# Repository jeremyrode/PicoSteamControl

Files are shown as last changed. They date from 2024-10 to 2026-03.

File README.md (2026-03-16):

# PicoSteamControl
This project implements a new Raspberry Pi Pico based control for a [Leisure Steam One Touch LS series steam generator](https://leisure-steam.com/product-category/steam-generators/1-touch-steam-unit/).

The factory control PCB was misbehaving, and I have wanted to implement an automatic self-flush to clean the tank, so I thought it would be a good challenge to replace it with a Raspberry Pi Pico.

This is my first MicroPython project.  I was originally implementing this system in C, but when I started down the path to connect a Pico W to WiFi, I decided to try out MicroPython and I was blown away by the power and rapid development/test cycles.

I mostly think this project might be interesting to people because of a few new ideas that I have not seen documented well in the wild:

# New ideas:

This project served as a testbed for 3 new ideas that I wanted to try:
- Status Logging and Timestamping though WiFi
- Capacitive Touch Sensing via a PIO State Machine
- New Ideal Diode Peak Detector CT Interface

## Status Logging and Timestamping though WiFi

A major reason I was implementing much of my IoT work with boards that run full Linux (usually a Raspberry Pi Zero W) is logging and timestamping functionality.  Many of these IoT systems are very difficult to debug without a persistent log that is timestamped.  Both storing and retrieving persistent logs (to some sort of nonvolatile memory) and getting real time (UTC) on a microcontroller are difficult.

Here, this is solved by sending my log messages out to Raspberry Pi with NTP running via the network and urequests libraries:

```python
def logWifi(logmessage):
    print('Log: ' + logmessage)
    res = requests.post(secrets.url, data = logmessage)
```

Remarkably simple and effective, this server could easily serve many Pico W boards. See main.py for the full code with WiFi reconnection, and error handling.  [The secrets.url uses a config file to not check in WiFi passwords or local IPs to a public Git.]( https://www.coderdojotc.org/micropython/wireless/02-connecting-to-wifi/ "MicroPython WiFi Info")

The logWifi() function in main.py takes the log request and sends it to a http server (SteamLogger.js) running in Node.js that timestamps it and writes it to a file.

```node
const server = http.createServer((req, res) => {
  if (req.method === 'POST') {
    let data = '';
    req.on('data', chunk => {
      data += chunk.toString();
    });
    req.on('end', () => {
      let curDate = new Date();
      let dateStr = curDate.toString();
      message = dateStr.slice(0,dateStr.length-33) + ' ' + data; //Prepend Time to message
      console.log(message);
      logfile.write(message + '\n')
      res.end('OK');
    });
  }
});
```
Note that this code was upgraded into batch mode via Gemini.

## Capacitive Touch Sensing via PIO State Machine

After discovering that the control button on the LS1 one touch is a capacitive membrane switch, I investigated specific ICs that detect capacitive touch sensing, but this is a perfect task for a PIO state machine. This PIO-based detection ended up very reliable and has very good dynamic range: Around 250K cycles for the untouched state, and with a strong push increasing this to 6-8M cycles.  A logging function serves to quantify the reliability. 

Here is a very unoptimized PIO state machine that charges a capacitive touch sensor via an output pin and a resistor, then cycle counts the time to discharge.
[I’ve broke this out into its own repository]( https://github.com/jeremyrode/RaspPiPicoTouchSensor "RaspPiPicoTouchSensor Repo"), and I might try to optimize it eventually.

```
pull(block)                 # Get charge delay val     
mov(x,osr)                  # Load charge delay val    
wrap_target()               # Only do the above once   
mov(y, invert(null))        # Set Y to Large (All Ones)
set(pins, 1)                # Start Charging           
label("innerloop")                                     
jmp(pin, "loopescape")      # If Pin is High, Escape   
jmp(y_dec, "innerloop")     # Loop and decrement Y     
label("loopescape")                                    
mov(isr,y)                  # Move Y to CPU SR         
set(pins, 0)                # Discharge                
push(noblock)               # Push Y                   
mov(y,x)                    # Load charge delay val    
label("chargeloop")                                    
jmp(y_dec, "chargeloop")     # If !Zero, X-- and loop  
wrap()                                                 
```

### How it Works

This code uses a PIO state machine to repeatedly charge and discharge the touch sensor detecting a change in capacitance via the time-to-charge.  The touch sensor is charged via an output pin connected through 1-megaohm resistor (R1 on schematic) giving a RC time delay that can be measured by an input pin connected directly to the touch sensor.

The PIO state machine starts by getting the discharge time via an initial value written to the PIO state machine, that is moved to scratch register X.  This is necessary, as the PIO SET instruction is limited to 31, which is nowhere near the necessary value* (1,250,000).  The state machine then sets Y to all ones, sets the charge pin to "1", and counts down (via the "innerloop") until the jump pin goes low via RC discharge.  The jump escapes the loop (via jumping to "loopescape").  The Y value is outputted by moving Y to the input shift register (ISR) and pushing to the FIFO.  The push is nonblocking, to keep the detections going, but the FIFO will go stale if it's not read periodically.  To prepare for the next detection the charge pin is set to discharge "0", and then the discharge delay is performed, but preserving the charge delay value stored in scratch register X, to Y, then looping via “chargeloop”.  At this point, we return to wrap_target(), which repeats everything (except loading the charge delay to scratch register X).

The user space code calibrates the baseline charge time with an IIR filter, and if a difference (here 4_000_000 cycles or 32 ms) in the charge time is detected a touch event is registered.  The touch detection is debounced via a time delay gate, as a single human-timescale touch event can trigger multiple PIO detections.

*Yes, I’m aware that large values in scratch registers can be set via the bit-reverse function of the MOV instruction, but these are a bit too large, as the smallest value is a SET of 16 (0b10000), bit reversed is 2^27, which is a delay of 1 second (2^27 / 125 MHz).

```python
baseline = 350_000 # Inital state for baseline IIR Value for touch detection (350_000, connected, 4_000 bare PCB)
touch_threshold = 4_000_000 #Threshold above baseline for a touch (4_000_000, connected, 4_000 bare PCB)
time_between_touches_ms = 1000 #Debounce time for a touch
DATA_IIR_CONST = 1000  # Filtering constant for the IIR filter
sm.put(1_250_000, 0)  #This sets Charging Delay and detection rate in SM clock cycles (10 ms)
while True:
    curval = 4_294_967_295 - sm.get() #State Machine counts down from 2^32
    if time.ticks_diff(time.ticks_ms(), last_touch) > time_between_touches_ms: #Not a multi-touch event
        if curval > baseline + touch_threshold: #We have a touch event
            last_touch = time.ticks_ms()
            print('Touch')
        else: #Only start taking button stats after the touch event has passed
            baseline = curval / DATA_IIR_CONST + baseline * (DATA_IIR_CONST - 1) / DATA_IIR_CONST #Take Baseline Stats
```

Here the python sets the discharge delay via sm.put().  An infinite loop pulls the discharge value and changes it into delay counts by subtracting from 2^32.  Here the detection is debounced via a timestamp and compared to a threshold value above a baseline non-touched value.  This code adapts the baseline capacitance via an infinite first-order impulse response (IIR) filter that adapts to any slow varying baseline capacitance.

## New Ideal Diode Peak Detector CT Interface

Interfacing to Current Transformers (CTs) is a real pain; either one needs to bias the signal in the middle of the ADC range, and sample fast enough to capture the 60 Hz sine wave, extracting the RMS, or a diode envelope detector can be used.  The simple diode envelope detector simplifies the ADC reading, as the output signal is DC, but the diode turn-on voltage makes the transfer function non-linear when the signal from the CT is below the diode turn-on voltage, making the current measurement inaccurate at low current.

Here, I’ve tried to make an ideal diode based peak detector (with gain) out of a non-inverting op amp driving though a diode.  Ideally this should both make the ADC readout much simpler and more accurate, as the output is DC, and the time constant can be set via a capacitor, and make the CT more accurate as the burden resistor can be sized optimally for the CT, with the op-amp gain used to optimally fill the ADC range from the typically lower voltage from a CT in the linear regime.

# Schematic:

The factory control board was replaced with a quad relay board from amazon, wired directly to a RJ45 (J2) breakout board from Spark Fun (Pins 8-3). This relay board replaces the factory control board, and is wired into the 220V fill solenoid, drain valve, and the 50A heater contactor.  The relay board is an active low (open collector) on pins 4-7, VCC on pin 4 and ground on pin 1.  I wired a 1600:1 50A Current Transformer (CT) to pins 1 and 2.

The factory touchpad with LED is wired to J1.  From measuring with a meter, the power LED is on Pins 1 and 2 of the RJ12 connector (J1).  The capacitive touch sensor is on pin 4.  I think the ground shield of the cap sensor is on pin 3.

Note that this is the schematic that I built on a proto board with parts on hand.  A PCB with a proper ground is in the PCB directory.

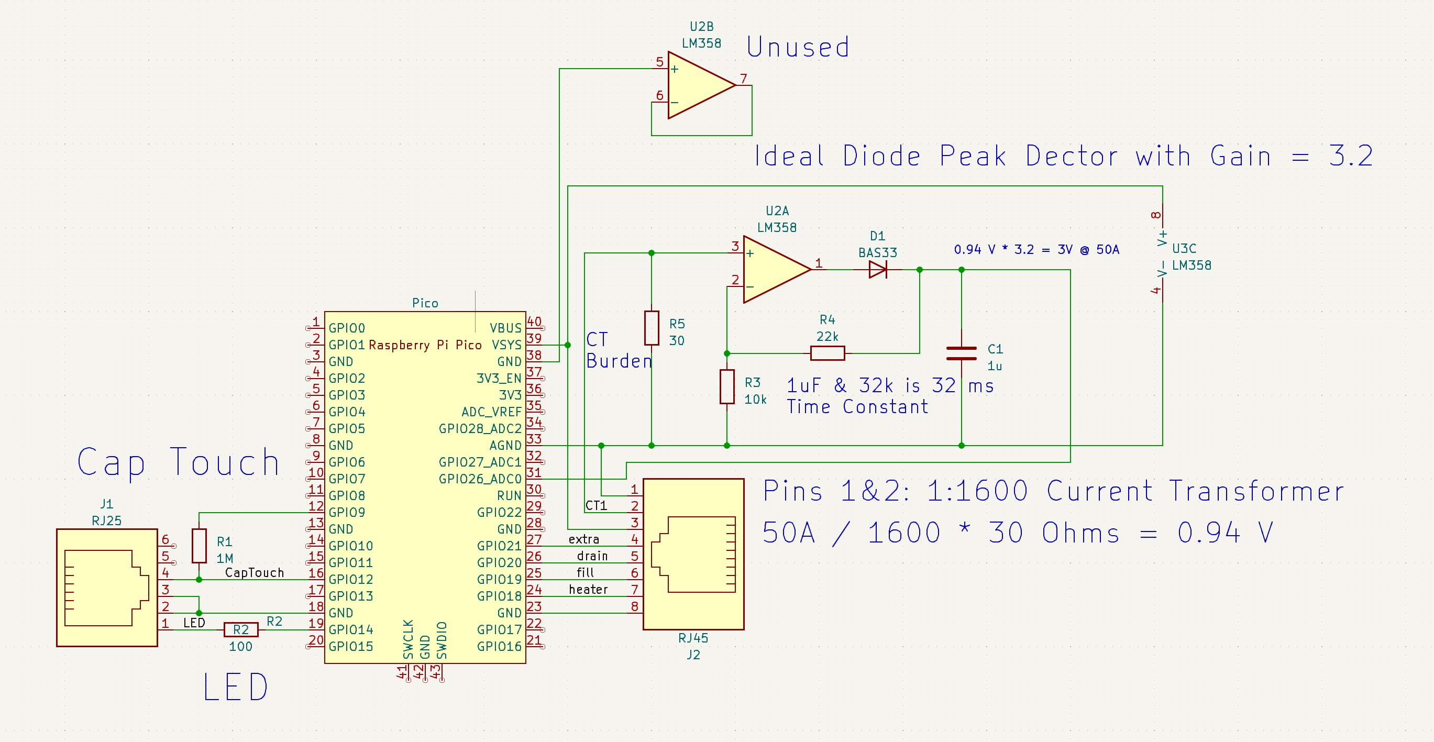
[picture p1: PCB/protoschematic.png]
Schematic


The CT burden resistor (R5) is set at 30 Ohms, calculated for good CT linearity.  The output voltage from the burdgen resistor goes to an op-amp (U2A). Here U2A with feedback around a diode (D1) forms an ideal diode, with feedback though a voltage divider formed by R4/R3, here with a voltage gain of 3.2X.  A 1uF capacitor (C1) stores the peak voltage from the diode (envelope detector), with a discharge time constant of ~32ms (1uF & 32k Ohms).  This voltage is converted by ADC0 of the Pico.

Testing and simulations show this time constant isn't nearly enough by a couple of orders of magnitude, the proper calculation should be how much voltage sag the sampling capacitor has over the 1/60 Hz cycle and this calculation results in the resistor sum greater than a megaohm for 1 LSB of a 12-bit ADC.  Achieving the time constant with larger values can cause opamp instability and overshoot when the current changes.

The unused is set to an non-inverting amp of gain 1 to ground, [as per recommendation.]( https://www.ti.com/lit/ab/sboa204a/sboa204a.pdf)  Note that the op amp used here needs to be rated for a common-mode voltage at the bottom rail (here ground), but not the top rail, as there is headroom between the 3.3V maximum output and the 5V supply.  The [LM358 is rated for VCM down to V- but only to V+ - 2V.](https://www.ti.com/product/LM358#tech-docs)

# Future Ideas
- Higher touch threshold for on than off
- Low/High via separate contactors for each heating element
- Optimize the PIO touch detection
- Single Pin touch detection

## Single Pin Optimized PIO touch detection

Single pin sans resistor touch detection is very possible.  The Pico has pin pull down functionality (it’s on by default), and the IO directionally can be set dynamically via PINDIRS.  The state machine could be made tighter by both slowing down the clock rate such that the delay can be implemented by the SET instruction, and the SIDESET functionality can save a few instructions.

# Errata Discovered for time.ticks_diff()

time.ticks_diff() doesn't seem to like intervals over a few days, the code was hanging.  I have changed the code to use a boolean to keep toggle the state, rather than rely on elapsed time, which seems to not work after a few days.

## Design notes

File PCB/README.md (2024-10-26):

# PicoSteamControl Schematic

No PCB yet, just the schematic I build on a protoboard

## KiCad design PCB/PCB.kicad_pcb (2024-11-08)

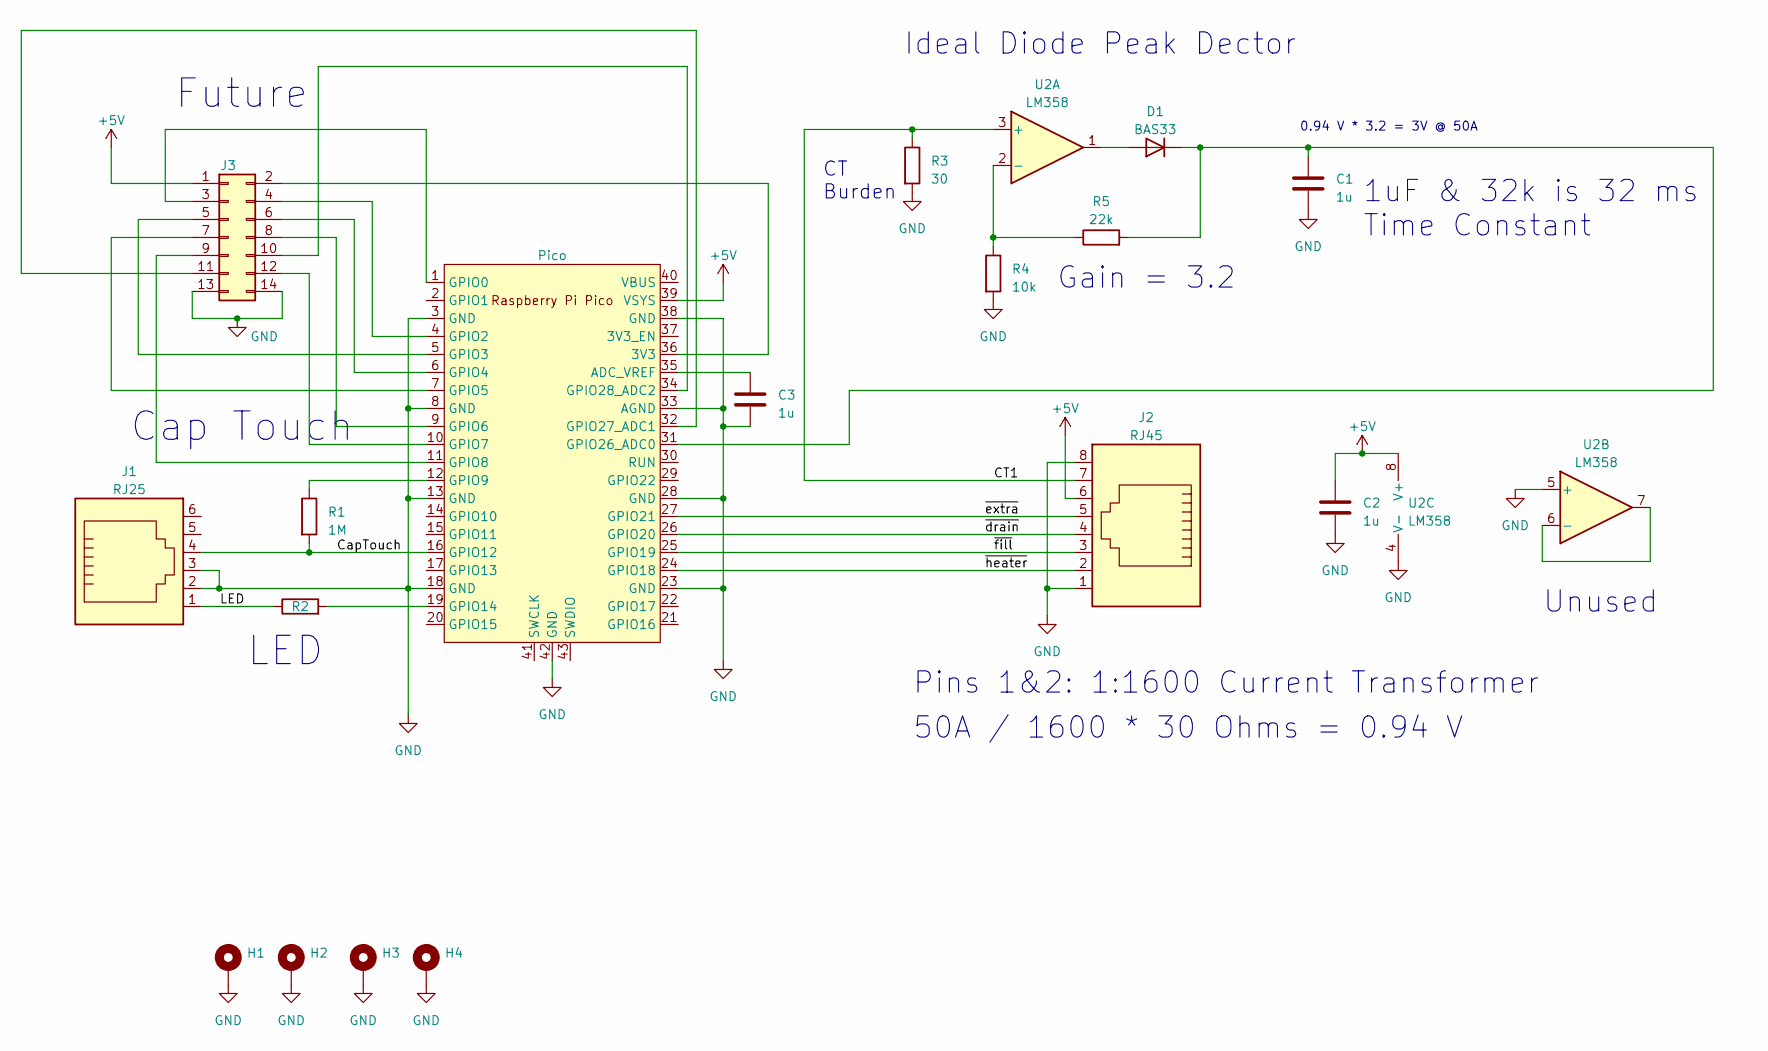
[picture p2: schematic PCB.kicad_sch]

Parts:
C1, C2, C3: 1u; C_0805_2012Metric_Pad1.18x1.45mm_HandSolder
D1: BAS33; D_DO-35_SOD27_P7.62mm_Horizontal
H1, H2, H3, H4: MountingHole_Pad; MountingHole_2.7mm_M2.5_Pad
J1: RJ25; RJ25_Wayconn_MJEA-660X1_Horizontal
J2: RJ45; RJ45_Amphenol_54602-x08_Horizontal
J3: Conn_2Rows-07Pins; PinHeader_2x07_P2.54mm_Vertical
R1: 1M; R_0805_2012Metric_Pad1.20x1.40mm_HandSolder
R2: 100; R_0805_2012Metric_Pad1.20x1.40mm_HandSolder
R3: 30; R_0805_2012Metric_Pad1.20x1.40mm_HandSolder
R4: 10k; R_0805_2012Metric_Pad1.20x1.40mm_HandSolder
R5: 22k; R_0805_2012Metric_Pad1.20x1.40mm_HandSolder
U1: Pico; RPi_Pico_SMD
U2: LM358; DIP-8_W10.16mm

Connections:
+5V: C2.1, J2.6, J3.1, U1.39 (VSYS), U2.8 (V+)
/CT1: J2.7, R3.1, U2.3 (+)
/CapTouch: J1.4, R1.2, U1.16 (GPIO12)
/LED: J1.1, R2.1
/~drain: J2.4, U1.26 (GPIO20)
/~extra: J2.5, U1.27 (GPIO21)
/~fill: J2.3, U1.25 (GPIO19)
/~heater: J2.2, U1.24 (GPIO18)
GND: C1.2, C2.2, C3.2, H1.1, H2.1, H3.1, H4.1, J1.2, J1.3, J2.1, J2.8, J3.13, J3.14, R3.2, R4.2, U1.3 (GND), U1.8 (GND), U1.13 (GND), U1.18 (GND), U1.23 (GND), U1.28 (GND), U1.33 (AGND), U1.38 (GND), U1.42 (GND), U2.4 (V-), U2.5 (+)
unnamed: D1.2 (A), U2.1
unnamed: C1.1, D1.1 (K), R5.2, U1.31 (GPIO26_ADC0)
unnamed: J3.2, U1.36 (3V3)
unnamed: J3.3, U1.1 (GPIO0)
unnamed: J3.4, U1.4 (GPIO2)
unnamed: J3.5, U1.5 (GPIO3)
unnamed: J3.6, U1.6 (GPIO4)
unnamed: J3.7, U1.7 (GPIO5)
unnamed: J3.8, U1.9 (GPIO6)
unnamed: J3.9, U1.11 (GPIO8)
unnamed: J3.10, U1.34 (GPIO28_ADC2)
unnamed: J3.11, U1.32 (GPIO27_ADC1)
unnamed: J3.12, U1.10 (GPIO7)
unnamed: C3.1, U1.35 (ADC_VREF)
unnamed: R1.1, U1.12 (GPIO9)
unnamed: R2.2, U1.19 (GPIO14)
unnamed: R4.1, R5.1, U2.2 (-)
unnamed: U2.6 (-), U2.7

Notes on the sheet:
Unused
1uF & 32k is 32 ms Time Constant
Ideal Diode Peak Dector
LED
Future
CT Burden
50A / 1600 * 30 Ohms = 0.94 V
Gain = 3.2
Cap Touch
0.94 V * 3.2 = 3V @ 50A
Pins 1&2: 1:1600 Current Transformer

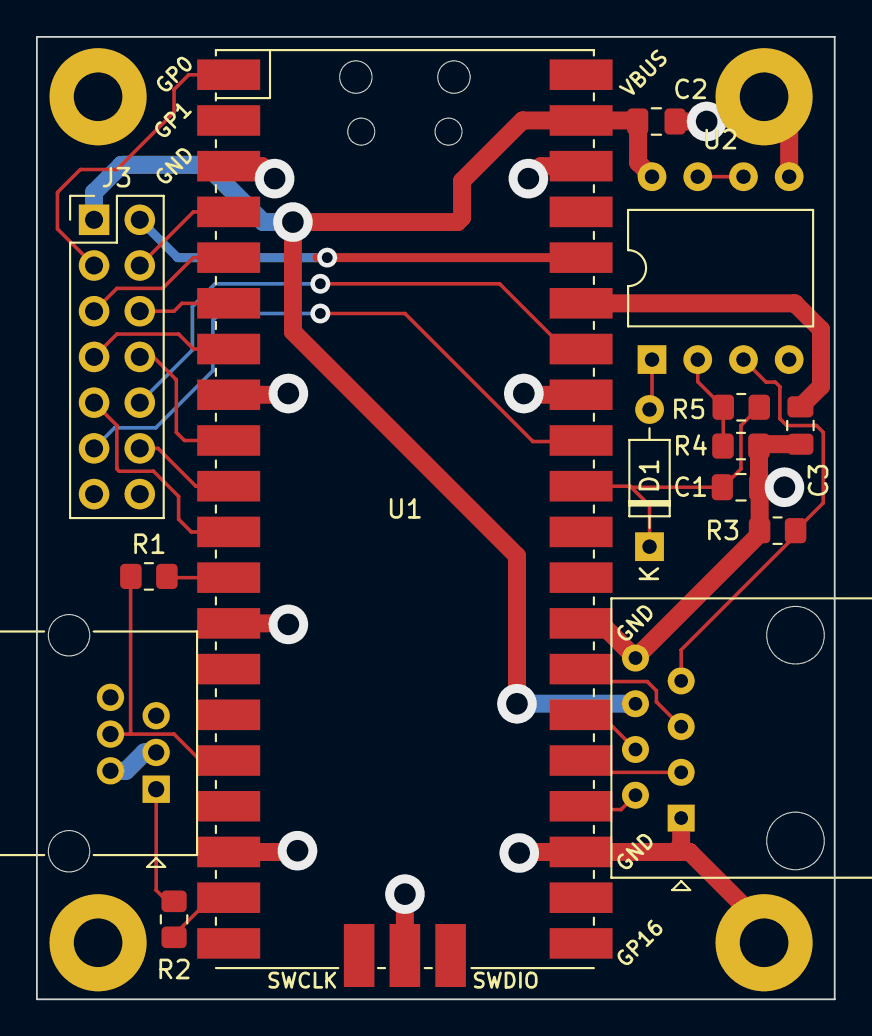
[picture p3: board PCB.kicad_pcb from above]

Board: 4 copper layers, 44.3 x 53.5 mm, 18 parts (0 on the bottom side), 27 nets.

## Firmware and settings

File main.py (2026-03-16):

import time
import machine
import rp2
import network
import secrets
import urequests as requests
print('boot')
## Pin Setup / LED
shower_led = machine.Pin(14, mode=machine.Pin.OUT, pull=None, value=0)
wled = machine.Pin("LED", machine.Pin.OUT) #Pico W LED
heater = machine.Pin(18, mode=machine.Pin.OPEN_DRAIN, pull=None, value=1)
fill = machine.Pin(19, mode=machine.Pin.OPEN_DRAIN, pull=None, value=1)
drain = machine.Pin(20, mode=machine.Pin.OPEN_DRAIN, pull=None, value=1)
extra =  machine.Pin(21, mode=machine.Pin.OPEN_DRAIN, pull=None, value=1)
# Turn off internal pull up on jmp pin
sense = machine.Pin(12, mode=machine.Pin.IN, pull=None)
adc = machine.ADC(machine.Pin(26))     # create ADC object on ADC pin
# Let us know were booting
wled.value(1)
shower_led.value(1)
# WLAN Setup
wlan = network.WLAN(network.STA_IF)
# Timers
statetimer = machine.Timer()
currentLogTimer = machine.Timer()
# Globals
state = 'off' # off / filling / heat / cool / flush / quickdrain
flush_count = 4 #Zero means flush done
log_queue = [] # Queue for log messages from timers
baseline = 350_000 # Inital state for baseline IIR Value for touch detection (350_000, connected, 4_000 bare PCB)
touch_threshold = 4_000_000 #Threshold above baseline for a touch (4_000_000, connected, 4_000 bare PCB)
time_between_touches_ms = 1000 #Debounce time for a touch
touch_armed = False
current_raw = 0 #Inital State for current IIR
DATA_IIR_CONST = 1000  # Filtering constant for the IIR filters
time_between_status_ms = 1000 * 60 * 60 * 12 # How often to log status
wifilog = True # If log to wifi
max_val = 0
# Helper to add to queue and print
def addLog(msg):
    print('Log:', msg)
    if len(log_queue) > 50:
        log_queue.pop(0) # Keep queue capped to protect RAM
    log_queue.append(msg)

# Logging Function
def flushWifiLogs(logmessage):
    if not wifilog:
        return True # Clear queue if logging is disabled

    if not wlan.isconnected():
        print(f"Reconnecting to WiFi Network Name: {secrets.ssid}")
        try:
            wlan.active(True)
            wlan.connect(secrets.ssid, secrets.password)
        except OSError as error:
            print(f'Connect error is {error}')
            return False
        except Exception as e:
            print(f"An unknown connect error occurred: {e}")
            return False
        print('Waiting for connection...')
        counter = 0
        while not wlan.isconnected():
            # wdt.feed()
            time.sleep(1)
            print(counter, '.', sep='', end='')
            counter += 1
            if counter > 20:
                print('Failed to Connect')
                return False
        print('\nIP Address: ', wlan.ifconfig()[0])
        
    try:
        print("Trying to Post")
        api_key = getattr(secrets, 'STEAM_LOGGER_SECRET_KEY', 'default_key')
        headers = {'x-api-key': api_key, 'Content-Type': 'text/plain'}
        res = requests.post(secrets.url, data=logmessage, headers=headers)
        print("Posted")
    except: #Need to catch this or we stop
        print("Log Failed, Post Error")
        return False
    else:
        success = False
        if res.text != 'OK':
            print('Unexpected Post Response:', res.text)
        else:
            success = True
        res.close()
        return success
    
# Helper functions to make code readable, and to add logging
def logCurrent(callingtimer):
    addLog(f"C: {round(current_raw)}")

def ledOn():
    wled.value(1) #Turn on board LED
    shower_led.value(1) #Turn on Shower LED

def ledOff():
    wled.value(0) #Turn off LED
    shower_led.value(0) #Turn off Shower LED

def heat_on():
    heater.value(0) #Turn on Heat, Active Low
    currentLogTimer.init(mode=machine.Timer.PERIODIC,period=30_000,callback=logCurrent) 

def heat_off():
    heater.value(1) #Turn off Heat, Active Low
    currentLogTimer.deinit() #No need to log anymore

def fill_open():
    fill.value(0) #Start Filling

def fill_closed():
    fill.value(1) #Stop Filling

def drain_open():
    drain.value(0) #Start Draining

def drain_closed():
    drain.value(1) #Stop Draining

def is_drain_closed():
    return drain.value()

# State Functions
def goFlush(callingtimer):
    global flush_count, state
    state = 'flush'
    fill_open() #Start Filling
    if not is_drain_closed(): #We are not draining
         drain_open() #Start Draining
         addLog(f"Flush Drain Cycle: {flush_count}")
    else:
        drain_closed() #Stop Draining
        flush_count -= 1 # Done with this flush round
        addLog(f"Flush Fill Cycle: {flush_count}")
    if flush_count > 0: #More flushes to go, recursive
        statetimer.init(mode=machine.Timer.ONE_SHOT,period=300_000,callback=goFlush) # Cycle the Flush 5 mins (300_000)
    else:
        addLog("Final Long Drain Cycle")
        drain_open() #Start Draining
        fill_closed()   # Stop Filling
        statetimer.init(mode=machine.Timer.ONE_SHOT,period=3_600_000,callback=goOff) # Final Drain Cycle 60 mins (3_600_000)
             
def goHeat(callingtimer):
    global state
    state = 'heat'
    ledOn() #Turn on LED
    fill_open() #Keep Filling
    heat_on() # Start Heat
    drain_closed() # Stop Drain
    statetimer.init(mode=machine.Timer.ONE_SHOT,period=900_000,callback=goCool) # Auto Off Timer 15 mins (900_000)
    addLog('Heat State')

def goCool(callingtimer):
    global flush_count, state
    state = 'cool'
    ledOff()
    fill_closed()   # Stop Filling
    heat_off() # Stop Heat
    drain_closed() # Stop Drain
    flush_count = 4 #Queue up some flushing
    statetimer.init(mode=machine.Timer.ONE_SHOT,period=3_600_000,callback=goFlush) # Cooling Timer 60 mins (3_600_000)
    addLog('Cool State')
    
def goFill(callingtimer):
    global state
    state = 'filling'
    ledOn() #Turn on LED
    fill_open() #Start Filling
    heat_off() # Stop Heat
    drain_closed() # Stop Drain
    statetimer.init(mode=machine.Timer.ONE_SHOT,period=20_000,callback=goHeat) # Fill Timer, 20s (20_000)
    addLog('Fill State')
   
def goOff(callingtimer):
    global state
    state = 'off'
    ledOff() #Turn off LED
    fill_closed()   # Stop Filling
    heat_off() # Stop Heat
    drain_closed() # Stop Drain
    statetimer.deinit()
    addLog('Off State')

def goQuickDrain(callingtimer):
    global state
    state = 'quickdrain'
    ledOff() #Turn off LED
    fill_closed()   # Stop Filling
    heat_off() # Stop Heat
    drain_open() #Start Draining
    statetimer.init(mode=machine.Timer.ONE_SHOT,period=600_000,callback=goOff) # Final Drain Cycle 10 mins (600_000)
    addLog('Quick Drain')
    
def printTouchStatus():
    global max_val, baseline, last_status
    addLog(f"Base: {round(baseline)} Max:  {round(max_val - baseline)}")
    max_val = 0
    last_status = time.ticks_ms()

# Touch Sensor PIO State Machine
@rp2.asm_pio(set_init=rp2.PIO.OUT_LOW, autopull=False, pull_thresh=32, autopush=False, push_thresh=32)
def detectTouch():                                         # type: ignore
    pull(block)                 # Get charge delay val     # type: ignore
    mov(x,osr)                  # Load charge delay val    # type: ignore
    wrap_target()               # Only do the above once   # type: ignore
    mov(y, invert(null))        # Set Y to Large (All Ones)# type: ignore
    set(pins, 1)                # Start Charging           # type: ignore
    label("innerloop")                                     # type: ignore
    jmp(pin, "loopescape")      # If Pin is High, Escape   # type: ignore
    jmp(y_dec, "innerloop")     # Loop and decrement Y     # type: ignore
    label("loopescape")                                    # type: ignore
    mov(isr,y)                  # Move Y to CPU SR         # type: ignore
    set(pins, 0)                # Discharge                # type: ignore
    push(noblock)               # Push Y                   # type: ignore
    mov(y,x)                    # Load charge delay val    # type: ignore
    label("chargeloop")                                    # type: ignore
    jmp(y_dec, "chargeloop")     # If !Zero, X-- and loop  # type: ignore
    wrap()                                                 # type: ignore
# Setup Code
# Create the State Machine, a 1 MegaOhm resistor from set_base to jmp_pin is needed
sm = rp2.StateMachine(0, detectTouch, freq=125_000_000, set_base=machine.Pin(9), jmp_pin=machine.Pin(12))
# Start the State Machine.
sm.active(1)
sm.put(1_250_000, 0)  #This sets Charging Delay and detection rate in SM clock cycles (10 ms)
# Let us know were done booting
# Start the Watchdog
# wdt = machine.WDT(timeout=8000)
addLog("Rebooted: v10 WiFi Logging Enabled")
wled.value(0)
shower_led.value(0)
last_touch = time.ticks_ms() # Limit immediate and back-to-back touch detections (debounce)
last_status = last_touch
while True: #Main loop
    curval = 4_294_967_295 - sm.get() #State Machine counts down from 2^32
    # Ticks_diff doesn't work well for more than a day, so make a sticky armed state
    if  touch_armed == False and time.ticks_diff(time.ticks_ms(), last_touch) > time_between_touches_ms: #Not a multi-touch event
        touch_armed = True # Only let time arm us, as the above will be false over long time periods
    if touch_armed:
        if curval > baseline + touch_threshold: #We have a touch event
            last_touch = time.ticks_ms() #States are: off / filling / heat / cool / flush / quickdrain
            if state == 'off' or state == 'flush' or state == 'quickdrain':
                goFill(0)
            elif state == 'heat':
                goCool(0)
            elif state == 'filling':
                goQuickDrain(0) # Someone shut us off before full
            elif state == 'cool':
                goHeat(0)
            else:
                goCool(0)
                addLog("Uh Oh, we fell though the state if")
            touch_armed = False;
            printTouchStatus()
            addLog(f"Press at: {round(curval - baseline)}")
        else: #Only start taking button stats after the touch event has passed
            baseline = curval / DATA_IIR_CONST + baseline * (DATA_IIR_CONST - 1) / DATA_IIR_CONST #Take Baseline Stats
            if curval > max_val: # Take some stats for logging
                max_val = curval
    # Do these things always
    current_raw  = adc.read_u16() / DATA_IIR_CONST + current_raw * (DATA_IIR_CONST - 1) / DATA_IIR_CONST
    #print status on an interval
    if time.ticks_diff(time.ticks_ms(), last_status) > time_between_status_ms:
        printTouchStatus()       
    
    # Process the log queue in the main loop instead of timers
    if log_queue:
        batched_messages = '\n'.join(log_queue)
        if flushWifiLogs(batched_messages):
            log_queue.clear()

    # wdt.feed()

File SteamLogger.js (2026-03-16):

"use strict";
const http = require('http');
const fs = require('fs');

const LOG_FILE = '/home/jprode/SteamControlLog.txt';
const PORT = 65432;
const API_KEY = 'STEAM_LOGGER_SECRET_KEY'; // Replace with a secure key in production

const logfile = fs.createWriteStream(LOG_FILE, { flags: 'a' });
logfile.on('error', (err) => {
  console.error('File stream error. Check permissions or path:', err);
});

const server = http.createServer((req, res) => {
  if (req.method !== 'POST') {
    res.writeHead(405, { 'Content-Type': 'text/plain' });
    res.end('Method Not Allowed: Send a POST request to this endpoint');
    console.log('Got something besides a POST:', req.method);
    return;
  }

  if (req.headers['x-api-key'] !== API_KEY) {
    res.writeHead(401, { 'Content-Type': 'text/plain' });
    res.end('Unauthorized');
    console.log('Unauthorized request access attempt from:', req.socket.remoteAddress);
    return;
  }

  let data = '';
  req.on('data', chunk => {
    data += chunk.toString();
    // Destroy connection if payload is too large (> 10KB)
    if (data.length > 10240) {
      res.writeHead(413, { 'Content-Type': 'text/plain' });
      res.end('Payload Too Large');
      req.connection.destroy();
    }
  });

  req.on('end', () => {
    if (res.writableEnded) return; // Ignore if response already destroyed
    let curDate = new Date();
    let dateStr = curDate.toLocaleString();
    let ip = req.headers['x-forwarded-for'] || req.socket.remoteAddress;

    // Process batch messages separated by newline
    let messages = data.split('\n').filter(msg => msg.trim() !== '');

    messages.forEach(msg => {
      let logLine = `${dateStr} [${ip}] ${msg}`;
      console.log(logLine);
      logfile.write(logLine + '\n');
    });

    res.writeHead(200, { 'Content-Type': 'text/plain' });
    res.end('OK');
  });
});

server.listen(PORT, () => {
  console.log('Server running on port ' + PORT);
  logfile.write('Started Server at ' + new Date().toLocaleString() + '\n');
});

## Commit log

2024-10-26 Testing Current Sensor, testing mode, add schematic
    [PCB.kicad_pcb, PCB.kicad_sch]
2024-10-27 Schematic and readme cleanup
    [PCB.kicad_sch]
2024-10-30 pcb updates
    [PCB.kicad_pcb, Proto_Board_as_Built.kicad_sch]
2024-11-08 gpio on PCB
    [PCB.kicad_pcb, PCB.kicad_sch]
2024-11-09 found schematic errors
    [Proto.kicad_pcb, Proto.kicad_sch, Proto_Board_as_Built.kicad_sch]
2024-11-09 more schematic changes
    [PCB.kicad_sch, Proto_Board_as_Built.kicad_sch]
2024-12-23 trying to fix button press not detected after a few days of idle
    [main.py]
2025-03-12 disabled wifi logging due to urequests crashing
    [main.py]
2026-03-14 Gemini Extensive Bug Fixes
    [SteamLogger.js, main.py]
